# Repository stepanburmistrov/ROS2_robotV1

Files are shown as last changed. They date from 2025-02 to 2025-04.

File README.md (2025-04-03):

# ROS2 Robot: Учебные материалы

Внешний вид робота

Тут собраны учебные материалы и примеры по разработке робота на **ROS2**.

## Изготовление и сборка робота
Робот может быть изготовлен из фанеры толщиной 6мм при помощи лазерной резки, или напечатан на 3д принтере. 
Звенья манипулятора изготавливаются из фанеры 4мм.
- [**Файлы доступны в форматах: SolidWorks 2022, STEP, DXF**](https://github.com/stepanburmistrov/ROS2_robotV1/tree/main/3D)

- [**Подробное описание выбора компонентов, методов сборки и используемых инструментов**](https://stepik.org/lesson/1590256/step/1?unit=1611795)

- [**Электрическая схема робота**](https://github.com/stepanburmistrov/ROS2_robotV1/blob/main/Circuit/ROS2_Robot_Circuit.pdf)
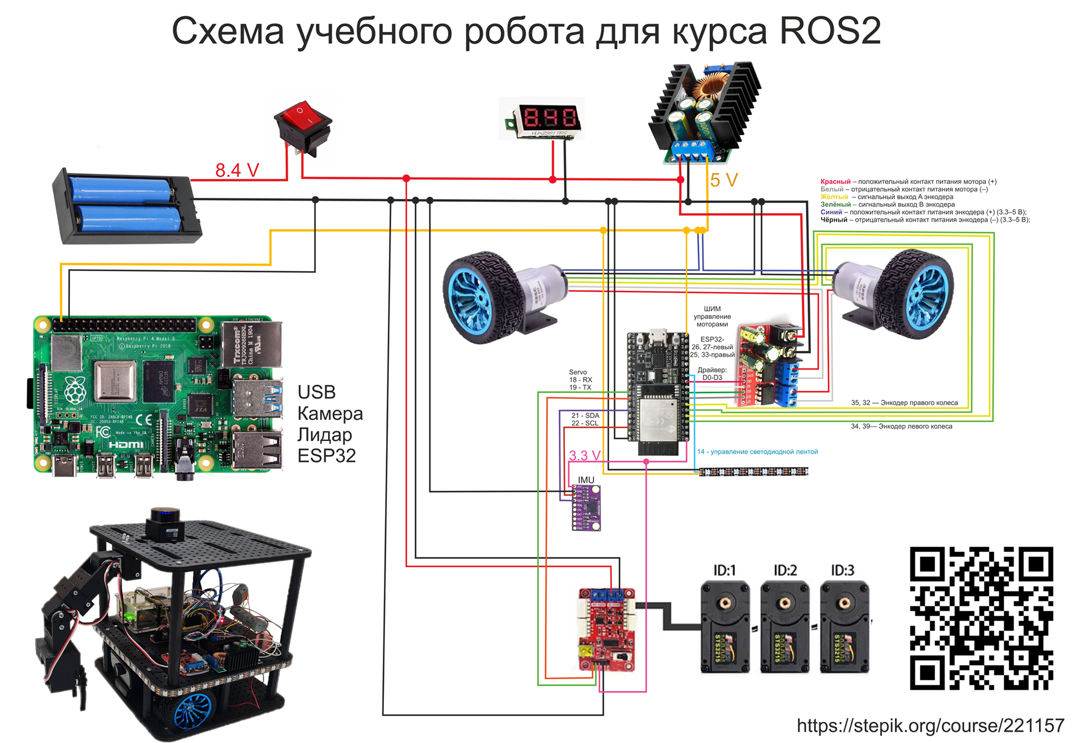
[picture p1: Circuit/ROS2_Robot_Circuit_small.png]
Электрическая схема робота


## Low-level на основе микроконтроллера ESP32
- [**Первые движения робота**](https://stepik.org/lesson/1590257/step/1?unit=1611796)
- [**Кинематика и расчет местоположения**](https://stepik.org/lesson/1590257/step/2?unit=1611796)
- [**Настройка PID-регуляторов**](https://stepik.org/lesson/1590257/step/4?unit=1611796)
- [**Линейная и угловая скорость робота**](https://stepik.org/lesson/1590257/step/7?unit=1611796)
- [**Световая индикация**](https://stepik.org/lesson/1590257/step/10?unit=1611796)
- [**Подключение IMU**](https://stepik.org/lesson/1590257/step/11?unit=1611796)
- [**Работа с сервоприводами манипулятора**](https://stepik.org/lesson/1590257/step/13?unit=1611796)

## Курс по ROS2
[**Бесплатный курс по ROS2**](https://stepik.org/course/221157):
- [**Установка Linux**](https://stepik.org/lesson/1505338/step/1?unit=1525484)
- [**Установка и запуск ROS2 Jazzy**](https://stepik.org/lesson/1505346/step/1?unit=1525492)
- [**Топик, паблишер, подписчик и другие средства коммуникации**](https://stepik.org/lesson/1597035/step/1?unit=1618661)
- [**Связь с LOW-LEVEL**](https://stepik.org/lesson/1590260/step/1?unit=1611799)
- [**RVIZ -  визуализация всего в роботе**](https://stepik.org/lesson/1612393/step/1?unit=1634192)
- [**Gazebo - симулятор робота с физикой**](https://stepik.org/lesson/1612395/step/1?unit=1634194)

Присоединяйтесь к курсу и улучшайте навыки программирования роботов, от базовой сборки до полноценной симуляции и автономной навигации!

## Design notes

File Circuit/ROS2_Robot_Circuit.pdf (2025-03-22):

8.4 V

# Схема учебного робота для курса ROS2

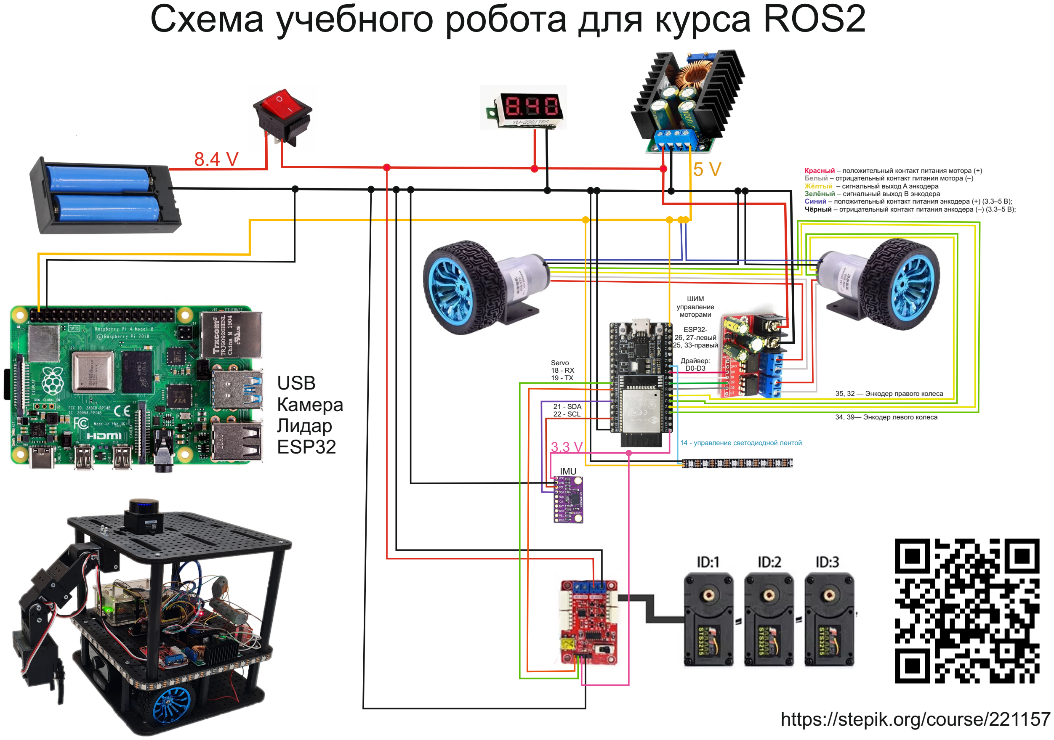
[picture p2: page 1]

ШИМ
управление
моторами

ESP32-
26, 27-левый
25, 33-правый

Драйвер:
D0-D3

34, 39— Энкодер левого колеса

35, 32 — Энкодер правого колеса

5 V | Красный – положительный контакт питания мотора (+)
| Белый – отрицательный контакт питания мотора (–) Жёлтый – сигнальный выход A энкодера Зелёный – сигнальный выход B энкодера Синий – положительный контакт питания энкодера (+) (3.3–5 В); Чёрный – отрицательный контакт питания энкодера (–) (3.3–5 В);

14 - управление светодиодной лентой

21 - SDA
22 - SCL

3.3 V

Servo
18 - RX
19 - TX USB

# Камера Лидар ESP32

## IMU

# https://stepik.org/course/221157

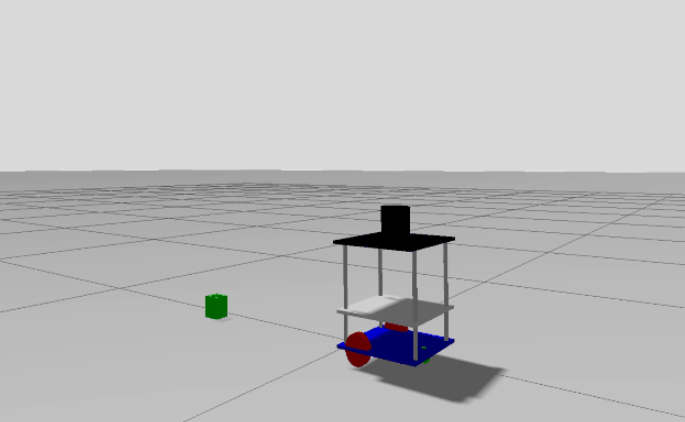
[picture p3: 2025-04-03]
3D/images/gazebo.png

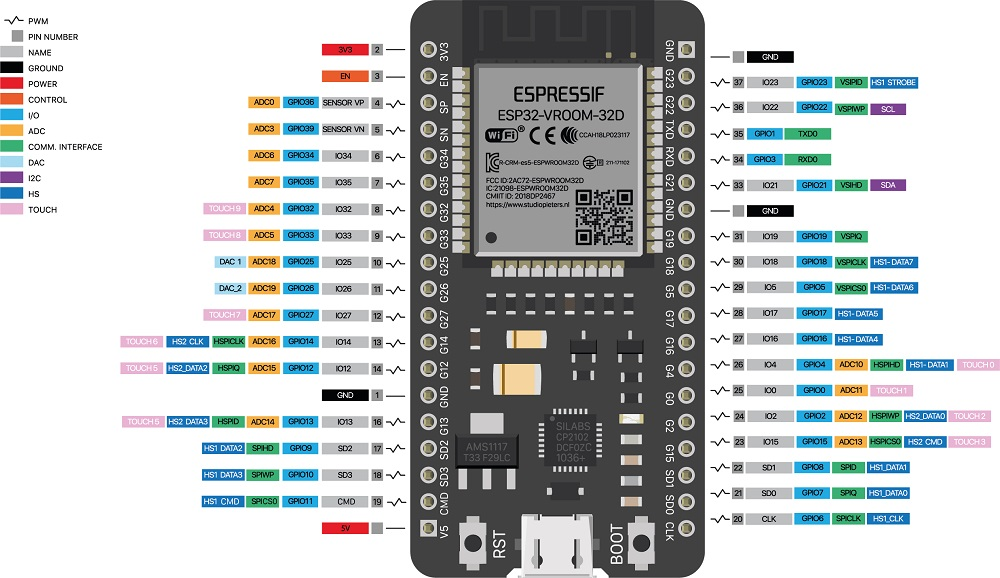
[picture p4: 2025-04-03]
3D/images/image.png

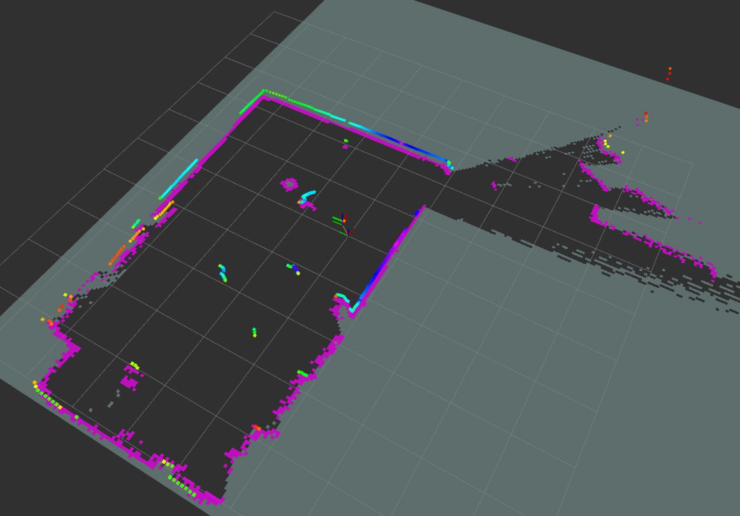
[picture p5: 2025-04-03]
3D/images/esp32.jpg

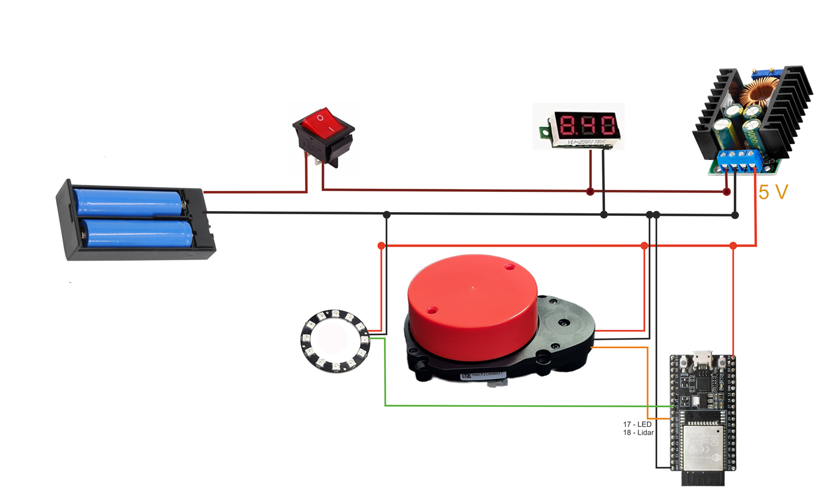
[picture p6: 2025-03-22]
3D/red_lidar_box/RedLidar_Circuit.png

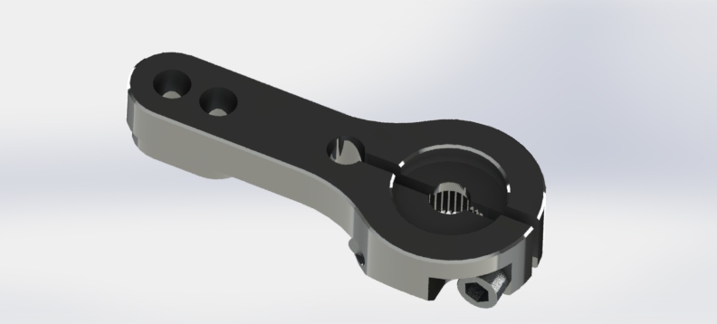
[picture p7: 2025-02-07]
3D/DS3225_MG_metal_horn/View2.JPG

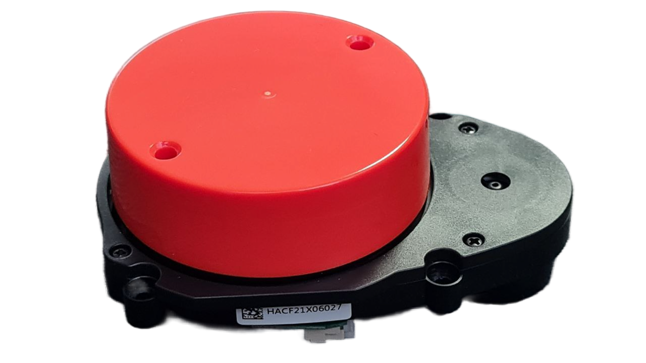
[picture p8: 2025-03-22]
3D/red_lidar_box/lidar.png

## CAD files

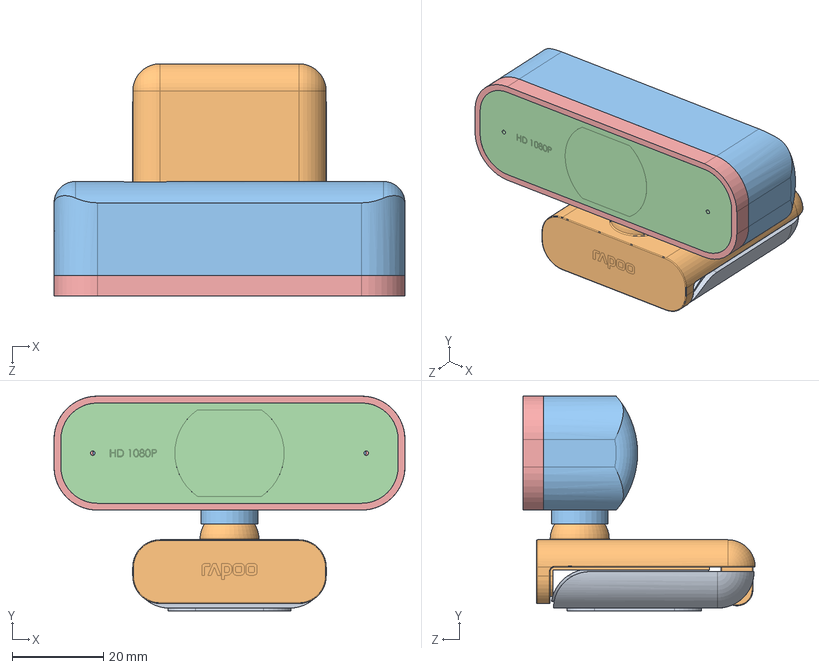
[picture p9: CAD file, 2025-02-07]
3D/webcam/C260 WebCam Assembly.SLDASM
77.0 x 47.1 x 51.0 mm
BaseC
Flexible Holder
Camera Casing
Auto Focus HD 1080p Lens
Lens Support
C260 WebCam
insert round nuts type a gb

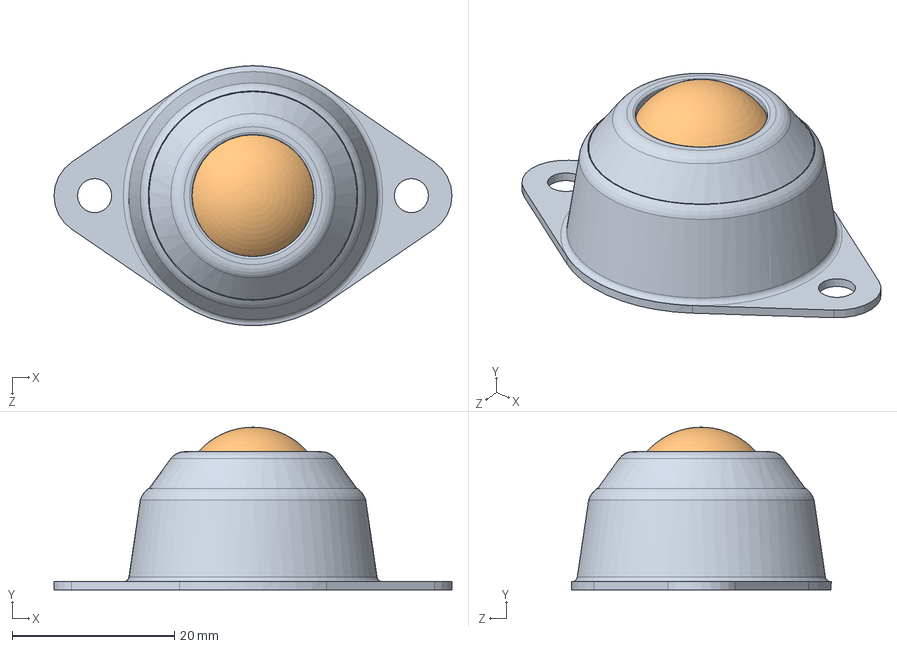
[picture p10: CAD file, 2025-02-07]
3D/Ball/Omni wheel steel ball OW007.SLDASM
49.0 x 20.0 x 32.0 mm
Base
Balle
Fond

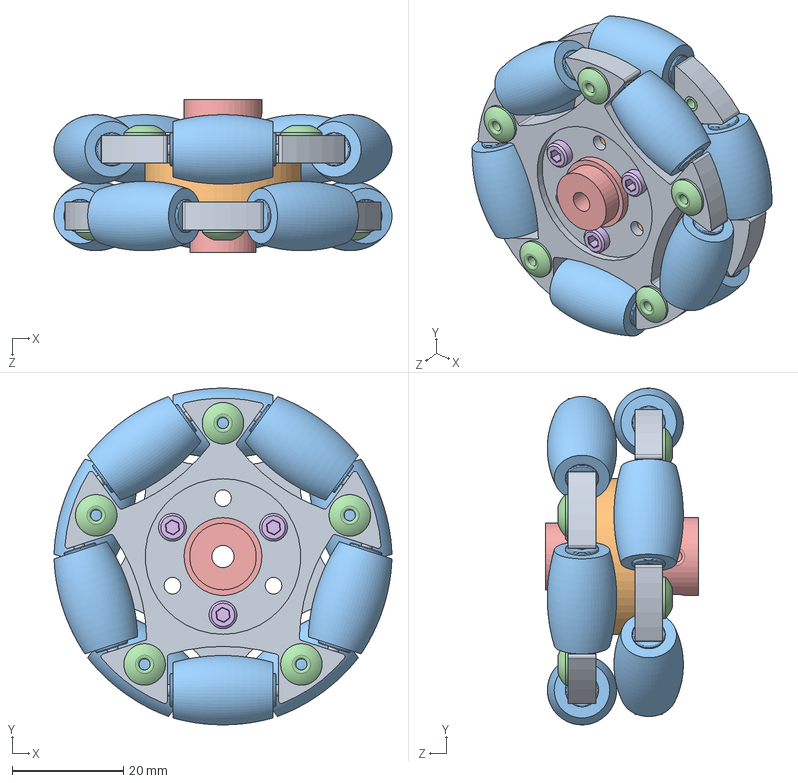
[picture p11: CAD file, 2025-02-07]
3D/Omni/WheelAsm.SLDASM
60.8 x 60.6 x 27.6 mm
WheelBase x 2
BasePlacer
RubberWheel x 10
Rivet x 10
ShaftConnector
M3HexNut x 6

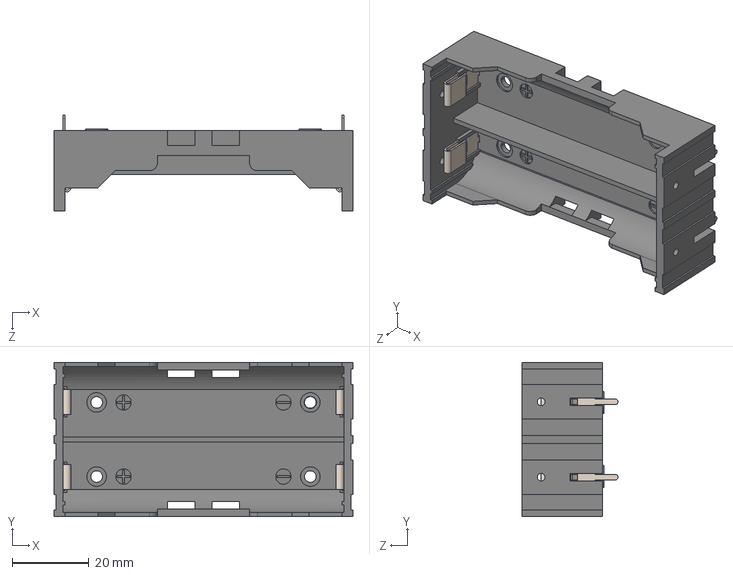
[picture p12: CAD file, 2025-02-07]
3D/18650holder/KLS5-18650-002-D.STEP
77.8 x 40.2 x 25.0 mm
KLS5-18650-002-D_Plastic
KLS5-18650-002-D_Me x 4

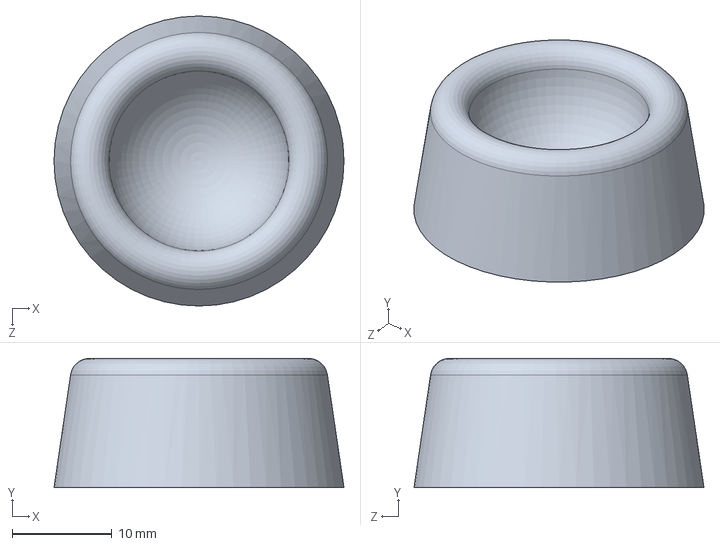
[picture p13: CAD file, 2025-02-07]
3D/Ball/Fond.SLDPRT
29.0 x 12.9 x 29.0 mm

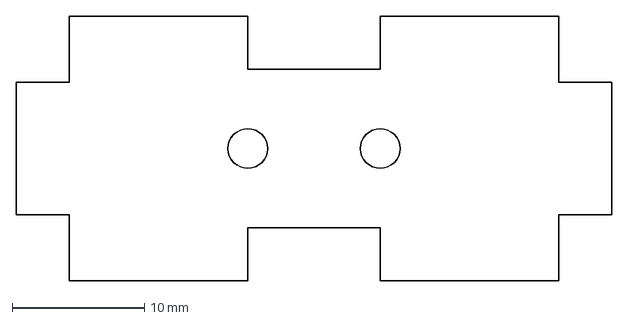
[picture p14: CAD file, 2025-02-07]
3D/dxf/4mm/ServoJointB.dxf
45.0 x 20.0 mm

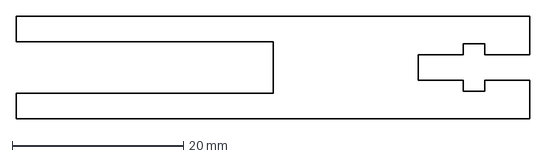
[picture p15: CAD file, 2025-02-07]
3D/dxf/6mm/LayerSupport65.dxf
60.0 x 12.0 mm

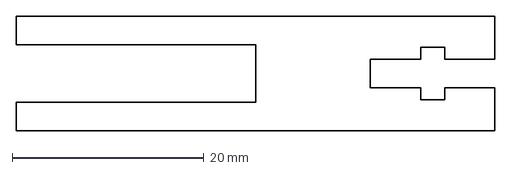
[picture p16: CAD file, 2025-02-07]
3D/dxf/ОпораГайка50.dxf
50.0 x 12.0 mm

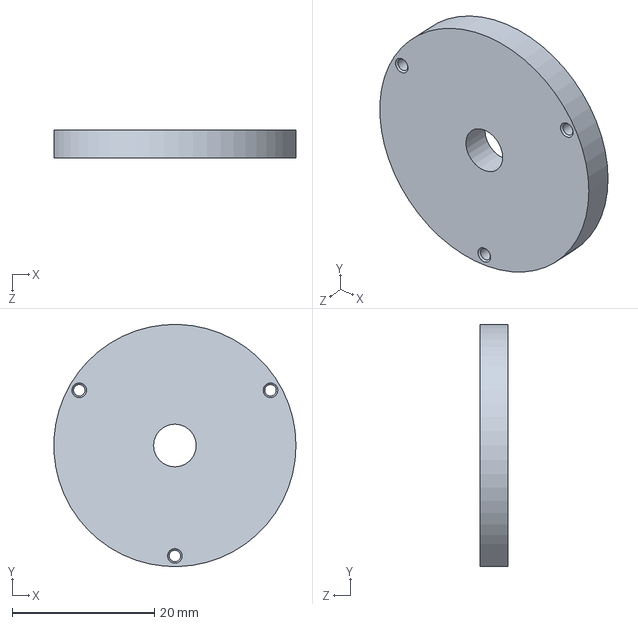
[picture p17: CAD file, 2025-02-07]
3D/jgb37/COUPLING BRACKET, GEARED BODY TO DC MOTOR, JGB37-520.SLDPRT
34.0 x 34.0 x 4.00 mm

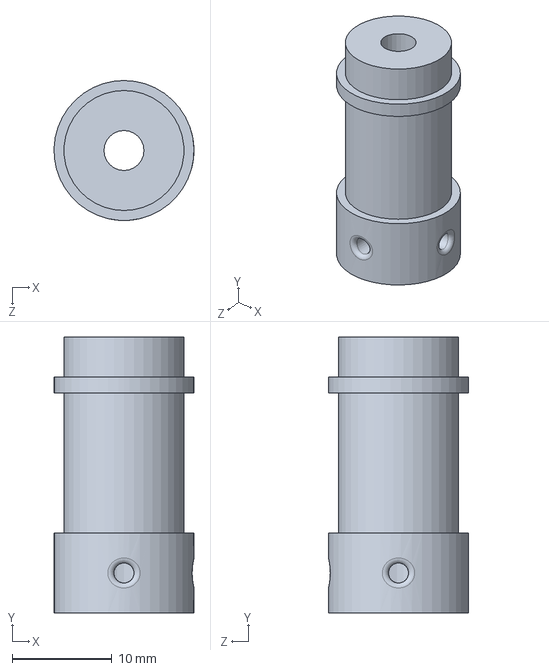
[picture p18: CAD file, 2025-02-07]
3D/Omni/ShaftConnector.SLDPRT
14.0 x 27.6 x 14.0 mm

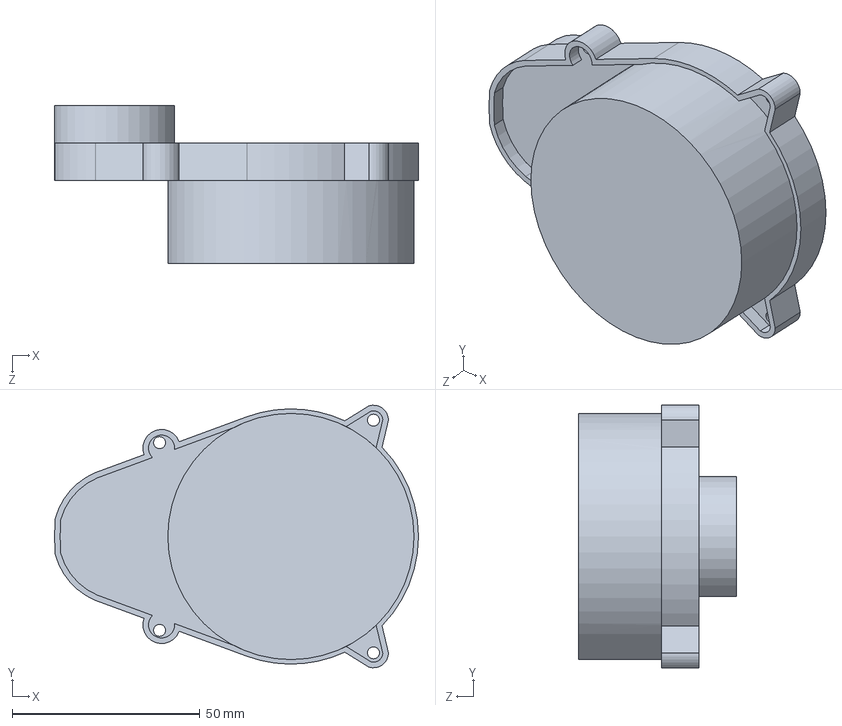
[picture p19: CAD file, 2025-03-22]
3D/red_lidar_box/ydlidar x4.SLDPRT
97.0 x 70.0 x 42.0 mm

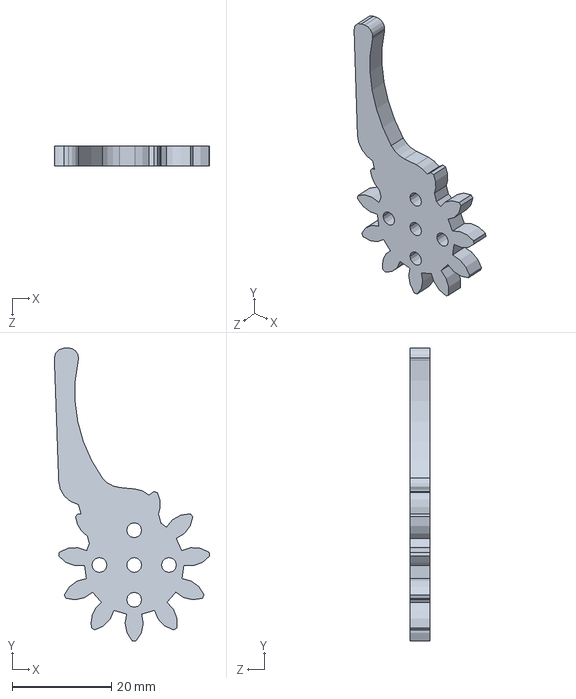
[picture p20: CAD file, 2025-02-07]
3D/STEP/GripperLeftGear.step.SLDPRT
31.3 x 59.0 x 4.00 mm

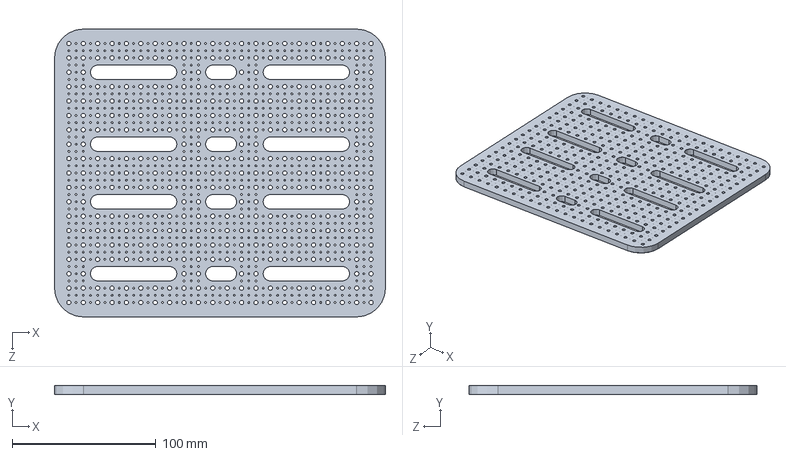
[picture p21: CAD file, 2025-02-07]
3D/TopLayer.SLDPRT
230.0 x 6.00 x 200.0 mm

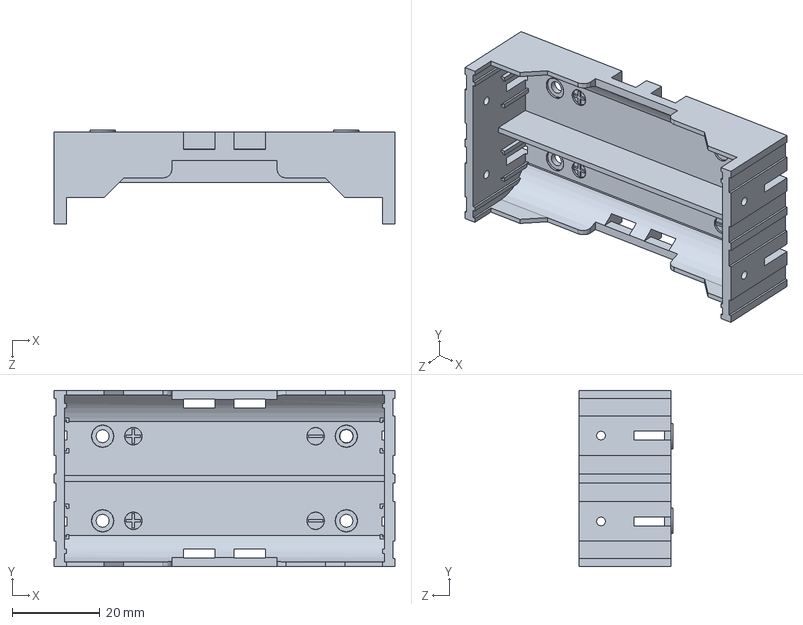
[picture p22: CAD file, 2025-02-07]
3D/18650holder/KLS5-18650-002-D_Plastic.SLDPRT
77.8 x 40.2 x 21.4 mm

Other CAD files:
3D/DS3225_MG_metal_horn/Assembly_DS3225MG_Metal_Horn.SLDASM
3D/Ball/Base.SLDPRT
3D/DS3225_MG_metal_horn/DS3225_MG_metal_horn.STEP
3D/dxf/4mm/BallWheelSupport.dxf
3D/18650holder/KLS5-18650-002-D.SLDASM
3D/18650holder/KLS5-18650-002-D_Me.SLDPRT
3D/Ball/Balle.SLDPRT
3D/BallWheelSupport.SLDPRT
3D/BaseLayer.SLDPRT
3D/DS3225_MG_metal_horn/DS3225_MG_metal_horn.SLDPRT
3D/DS3225_MG_metal_horn/screw_M2x8mm.SLDPRT
3D/DS3225_MG_metal_horn/screw_M2x8mm.STEP
3D/GripperLeftGear.SLDPRT
3D/GripperPlateA.SLDPRT
3D/GripperPlateB.SLDPRT
3D/GripperPlateBack.SLDPRT
3D/GripperPlateBottomSide.SLDPRT
3D/GripperRightGear.SLDPRT
3D/GripperServoHorn.SLDPRT
3D/GripperSide.SLDPRT
3D/L298N.SLDPRT
3D/Layer.SLDPRT
3D/LayerSupport130.SLDPRT
3D/LayerSupport65.SLDPRT
3D/OMNISupport.SLDPRT
3D/Omni/BasePlacer.SLDPRT
3D/Omni/M3HexNut.SLDPRT
3D/Omni/Rivet.SLDPRT
3D/Omni/RubberWheel.SLDPRT
3D/Omni/WheelBase.SLDPRT
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

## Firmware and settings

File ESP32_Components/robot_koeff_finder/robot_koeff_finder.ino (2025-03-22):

// Определение пинов, переменных энкодеров, положения робота и т.д.
#define LEFT_MOTOR_A 27     
#define LEFT_MOTOR_B 26     
#define RIGHT_MOTOR_A 25    
#define RIGHT_MOTOR_B 33    

#define LEFT_ENCODER_A 39    
#define LEFT_ENCODER_B 34    
#define RIGHT_ENCODER_A 32   
#define RIGHT_ENCODER_B 35   

volatile long left_encoder_value = 0; 
volatile long right_encoder_value = 0;
long last_left_encoder = 0;
long last_right_encoder = 0;

long last_speed_left_encoder = 0, last_speed_right_encoder = 0;
float leftWheelSpeed = 0.0, rightWheelSpeed = 0.0;
float vlSpeedFiltered = 0.0, vrSpeedFiltered = 0.0;
uint32_t lastTimeL = 0, lastTimeR = 0;

float targetLeftWheelSpeed = 0, targetRightWheelSpeed = 0;

float xPos = 0.0, yPos = 0.0, theta = 0.0;

const float WHEEL_DIAMETER = 69.0;
const float WHEEL_BASE = 185.0;
const float ENCODER_RESOLUTION = 330.0;
const float TICKS_TO_MM = (PI * WHEEL_DIAMETER) / ENCODER_RESOLUTION;
const float ALPHA = 0.5; // Коэффициент фильтрации скорости

// Глобальные коэффициенты PID – их можно обновлять через UART
float pidKp = 1.1;
float pidKi = 1.3;
float pidKd = 0.01;
float pidKff = 0.25;

void left_interrupt() {
  digitalRead(LEFT_ENCODER_B) ? left_encoder_value++ : left_encoder_value--;
}
void right_interrupt() {
  digitalRead(RIGHT_ENCODER_B) ? right_encoder_value++ : right_encoder_value--;
}

void updateOdometry() {
  long deltaLeft = left_encoder_value - last_left_encoder;
  long deltaRight = right_encoder_value - last_right_encoder;
  last_left_encoder = left_encoder_value;
  last_right_encoder = right_encoder_value;

  float distLeft = deltaLeft * TICKS_TO_MM;
  float distRight = deltaRight * TICKS_TO_MM;
  float deltaS = (distLeft + distRight) / 2.0;
  float deltaTheta = (distRight - distLeft) / WHEEL_BASE;

  theta += deltaTheta;
  xPos += deltaS * cos(theta);
  yPos += deltaS * sin(theta);
}

void computeSpeed() {
  uint32_t now = micros();

  if (lastTimeL == 0 || lastTimeR == 0) { 
    lastTimeL = now;
    lastTimeR = now;
    last_speed_left_encoder = left_encoder_value;
    last_speed_right_encoder = right_encoder_value;
    return;
  }

  float dtL = (now - lastTimeL) * 0.000001;
  float dtR = (now - lastTimeR) * 0.000001;

  if (dtL > 0 && left_encoder_value != last_speed_left_encoder) {
    long deltaLeft = left_encoder_value - last_speed_left_encoder;
    float wlSpeed = ((float)deltaLeft / ENCODER_RESOLUTION) * 360.0f / dtL;
    float vlSpeed = (wlSpeed / 360.0f) * (PI * WHEEL_DIAMETER);
    vlSpeedFiltered = ALPHA * vlSpeed + (1.0f - ALPHA) * vlSpeedFiltered;
    last_speed_left_encoder = left_encoder_value;
    lastTimeL = now;
  } else if (dtL > 0.005 && left_encoder_value == last_speed_left_encoder){
    vlSpeedFiltered = 0;
  }

  if (dtR > 0 && right_encoder_value != last_speed_right_encoder) {
    long deltaRight = right_encoder_value - last_speed_right_encoder;
    float wrSpeed = ((float)deltaRight / ENCODER_RESOLUTION) * 360.0f / dtR;
    float vrSpeed = (wrSpeed / 360.0f) * (PI * WHEEL_DIAMETER);
    vrSpeedFiltered = ALPHA * vrSpeed + (1.0f - ALPHA) * vrSpeedFiltered;
    last_speed_right_encoder = right_encoder_value;
    lastTimeR = now;
  } else if (dtR > 0.005 && right_encoder_value == last_speed_right_encoder){
    vrSpeedFiltered = 0;
  }
}

void computeWheelsPID(){
  // Ограничение интегральной составляющей (anti-windup)
  const float integralLimit = 100.0;

  // Статические переменные для состояния PID для каждого колеса
  static float errorLeftIntegral = 0;
  static float errorRightIntegral = 0;
  static float prevErrorLeft = 0;
  static float prevErrorRight = 0;
  static uint32_t lastPIDTime = millis();
  // Для сброса интегральной составляющей при смене целевой скорости
  static float lastTargetLeft = 0.0;
  static float lastTargetRight = 0.0;

  // Сброс интеграла, если целевая скорость изменилась
  if(targetLeftWheelSpeed != lastTargetLeft){
    errorLeftIntegral = 0;
    prevErrorLeft = 0;
    lastTargetLeft = targetLeftWheelSpeed;
  }
  if(targetRightWheelSpeed != lastTargetRight){
    errorRightIntegral = 0;
    prevErrorRight = 0;
    lastTargetRight = targetRightWheelSpeed;
  }

  // Вычисляем интервал dt (в секундах)
  uint32_t now = millis();
  float dt = (now - lastPIDTime) / 1000.0f;
  if(dt < 0.001f) dt = 0.001f;
  lastPIDTime = now;

  // Расчет ошибок
  float errorLeft  = targetLeftWheelSpeed  - vlSpeedFiltered;
  float errorRight = targetRightWheelSpeed - vrSpeedFiltered;

  // Интегральная составляющая
  errorLeftIntegral  += errorLeft  * dt;
  errorRightIntegral += errorRight * dt;
  if(errorLeftIntegral > integralLimit)  errorLeftIntegral  = integralLimit;
  if(errorLeftIntegral < -integralLimit) errorLeftIntegral  = -integralLimit;
  if(errorRightIntegral > integralLimit)  errorRightIntegral = integralLimit;
  if(errorRightIntegral < -integralLimit) errorRightIntegral = -integralLimit;

  // Производная ошибки
  float derivativeLeft  = (errorLeft  - prevErrorLeft)  / dt;
  float derivativeRight = (errorRight - prevErrorRight) / dt;
  prevErrorLeft  = errorLeft;
  prevErrorRight = errorRight;

  // Вычисление PID-выхода с использованием глобальных коэффициентов
  float pidLeft  = pidKp * errorLeft  + pidKi * errorLeftIntegral  + pidKd * derivativeLeft;
  float pidRight = pidKp * errorRight + pidKi * errorRightIntegral + pidKd * derivativeRight;

  // Добавляем feedforward
  float outputLeft  = pidLeft  + pidKff * targetLeftWheelSpeed;
  float outputRight = pidRight + pidKff * targetRightWheelSpeed;

  // Преобразование в значения ШИМ
  int leftA_PWM = 0, leftB_PWM = 0;
  int rightA_PWM = 0, rightB_PWM = 0;

  if(outputLeft >= 0){
    leftA_PWM = 0;
    leftB_PWM = constrain((int)outputLeft, 0, 255);
  } else {
    leftA_PWM = constrain((int)(-outputLeft), 0, 255);
    leftB_PWM = 0;
  }
  if(outputRight >= 0){
    rightA_PWM = 0;
    rightB_PWM = constrain((int)outputRight, 0, 255);
  } else {
    rightA_PWM = constrain((int)(-outputRight), 0, 255);
    rightB_PWM = 0;
  }

  setMotorsPWM(leftA_PWM, leftB_PWM, rightA_PWM, rightB_PWM);
}

void setMotorsPWM(int leftA, int leftB, int rightA, int rightB) {
  leftA  = constrain(leftA, 0, 255);
  leftB  = constrain(leftB, 0, 255);
  rightA = constrain(rightA, 0, 255);
  rightB = constrain(rightB, 0, 255);

  analogWrite(LEFT_MOTOR_A, leftA);
  analogWrite(LEFT_MOTOR_B, leftB);
  analogWrite(RIGHT_MOTOR_A, rightA);
  analogWrite(RIGHT_MOTOR_B, rightB);
}

// Функция для парсинга команды установки коэффициентов: "SET_COEFF Kp Ki Kd Kff"
bool parseSetCoeff(const String& command, float* Kp, float* Ki, float* Kd, float* Kff) {
  int index1 = command.indexOf(' ');
  if(index1 == -1) return false;
  int index2 = command.indexOf(' ', index1 + 1);
  if(index2 == -1) return false;
  int index3 = command.indexOf(' ', index2 + 1);
  if(index3 == -1) return false;
  int index4 = command.indexOf(' ', index3 + 1);
  if(index4 == -1) return false;

  *Kp = command.substring(index1 + 1, index2).toFloat();
  *Ki = command.substring(index2 + 1, index3).toFloat();
  *Kd = command.substring(index3 + 1, index4).toFloat();
  *Kff = command.substring(index4 + 1).toFloat();
  return true;
}

// Другие функции парсинга команд (SET_PWM, SET_POSE, SET_WHEELS_SPEED) аналогичны предыдущим примерам
bool parseSetPWM(const String& command, int* leftA_PWM, int* leftB_PWM, int* rightA_PWM, int* rightB_PWM) {
  int index1 = command.indexOf(' ');
  if (index1 == -1) return false;
  int index2 = command.indexOf(' ', index1 + 1);
  if (index2 == -1) return false;
  int index3 = command.indexOf(' ', index2 + 1);
  if (index3 == -1) return false;
  int index4 = command.indexOf(' ', index3 + 1);
  if (index4 == -1) return false;

  *leftA_PWM = command.substring(index1 + 1, index2).toInt();
  *leftB_PWM = command.substring(index2 + 1, index3).toInt();
  *rightA_PWM = command.substring(index3 + 1, index4).toInt();
  *rightB_PWM = command.substring(index4 + 1).toInt();
  return true;
}
bool parseSetSpeed(const String& command, int* speedLeft, int* speedRight) {
  int index1 = command.indexOf(' ');
  if (index1 == -1) return false;
  int index2 = command.indexOf(' ', index1 + 1);
  if (index2 == -1) return false;

  *speedLeft = command.substring(index1 + 1, index2).toInt();
  *speedRight = command.substring(index2 + 1).toInt();
  return true;
}

void processCommand(String command) {
  command.trim();
  if (command.startsWith("SET_PWM")) {
    int leftA_PWM = 0, leftB_PWM = 0, rightA_PWM =0, rightB_PWM = 0;
    if (parseSetPWM(command, &leftA_PWM, &leftB_PWM, &rightA_PWM, &rightB_PWM)) {
      setMotorsPWM(leftA_PWM, leftB_PWM, rightA_PWM, rightB_PWM);
      Serial.println("OK: Set PWM");
    }
  } else if (command.startsWith("SET_POSE")) {
    float x, y, th;
    // Парсинг команды SET_POSE аналогичен предыдущему примеру
    // …
    Serial.println("OK: Pose set");
  } else if (command.startsWith("SET_WHEELS_SPEED")) {
    int leftSpeed = 0, rightSpeed = 0;
    if (parseSetSpeed(command, &leftSpeed, &rightSpeed)) {
      targetLeftWheelSpeed = leftSpeed;
      targetRightWheelSpeed = rightSpeed;
      Serial.println("OK: Wheel speed set");
    }
  } else if (command.startsWith("SET_COEFF")) {
    float newKp, newKi, newKd, newKff;
    if (parseSetCoeff(command, &newKp, &newKi, &newKd, &newKff)) {
      pidKp = newKp;
      pidKi = newKi;
      pidKd = newKd;
      pidKff = newKff;
      Serial.println("OK: Coefficients updated");
    } else {
      Serial.println("ERROR: Invalid coefficients");
    }
  } else {
    Serial.println("ERROR: Unknown command");
  }
}

void setup() {
  Serial.begin(115200);
  delay(1000);
  Serial.println("System started");

  attachInterrupt(digitalPinToInterrupt(LEFT_ENCODER_A), left_interrupt, RISING);
  attachInterrupt(digitalPinToInterrupt(RIGHT_ENCODER_A), right_interrupt, RISING);
  
  pinMode(LEFT_MOTOR_A, OUTPUT);
  pinMode(LEFT_MOTOR_B, OUTPUT);
  pinMode(RIGHT_MOTOR_A, OUTPUT);
  pinMode(RIGHT_MOTOR_B, OUTPUT);
  
  pinMode(LEFT_ENCODER_A, INPUT);
  pinMode(LEFT_ENCODER_B, INPUT);
  pinMode(RIGHT_ENCODER_A, INPUT);
  pinMode(RIGHT_ENCODER_B, INPUT);
}

void loop() {
  if (Serial.available()) {
    String command = Serial.readStringUntil('\n');
    processCommand(command);
  }
  

  static uint32_t PIDTimer = 0;
  if (millis() - PIDTimer > 50) {
    computeSpeed();
    updateOdometry();
    computeWheelsPID();
    PIDTimer = millis();
  }

  static uint32_t printTimer = 0;
  if (millis() - printTimer > 200) {
    Serial.printf("POS X=%.2f Y=%.2f Th=%.2f ", xPos, yPos, theta);
    Serial.printf("ENC L=%ld R=%ld ", left_encoder_value, right_encoder_value);
    Serial.printf("SPD L=%.2f mm/s R=%.2f mm/s ", vlSpeedFiltered, vrSpeedFiltered);
    Serial.printf("Target L=%.2f mm/s R=%.2f mm/s\n", targetLeftWheelSpeed, targetRightWheelSpeed);
    printTimer = millis();
  }
}

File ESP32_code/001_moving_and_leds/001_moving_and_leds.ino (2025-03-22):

#include <Adafruit_NeoPixel.h>
#include <SCServo.h>
// Класс для управления STS-сервами (FEETECH STS3215 и т.д.)
SMS_STS st;

// Пины UART (приведён пример для ESP32 с UART1, GPIO 18/19).
#define S_RXD 18
#define S_TXD 19

// Скорость UART для серво
#define SERVO_BAUD 1000000

// ------------------------- НАСТРОЙКИ СВЕТОДИОДНОЙ ЛЕНТЫ -------------------------
#define PIN_WS2812B 14     // Пин, к которому подключена лента
#define NUM_PIXELS 50      // Кол-во светодиодов в ленте
#define LED_BRIGHTNESS 50  // Базовая «глобальная» яркость (0-255), если нужно

Adafruit_NeoPixel ws2812b(NUM_PIXELS, PIN_WS2812B, NEO_GRB + NEO_KHZ800);

uint8_t bootMode = 1;
// ---------------------------------------------------------------------------------

/****************************************************************************
 * Определение пинов, переменных энкодеров, положения робота и т.д.
 ***************************************************************************/
#define LEFT_MOTOR_A 27
#define LEFT_MOTOR_B 26
#define RIGHT_MOTOR_A 25
#define RIGHT_MOTOR_B 33

#define LEFT_ENCODER_A 39
#define LEFT_ENCODER_B 34
#define RIGHT_ENCODER_A 32
#define RIGHT_ENCODER_B 35

volatile long left_encoder_value = 0;
volatile long right_encoder_value = 0;
long last_left_encoder = 0;
long last_right_encoder = 0;

long last_speed_left_encoder = 0, last_speed_right_encoder = 0;
float vlSpeedFiltered = 0.0, vrSpeedFiltered = 0.0;
uint32_t lastTimeL = 0, lastTimeR = 0;

float targetLeftWheelSpeed = 0, targetRightWheelSpeed = 0;

float xPos = 0.0, yPos = 0.0, theta = 0.0;

const float WHEEL_DIAMETER = 69.0;       // мм
const float WHEEL_BASE = 185.0;          // мм (расстояние между центрами колёс)
const float ENCODER_RESOLUTION = 330.0;  // тиков на оборот
const float TICKS_TO_MM = (PI * WHEEL_DIAMETER) / ENCODER_RESOLUTION;
const float ALPHA = 0.5;  // Коэффициент экспоненциальной фильтрации скорости

// Глобальные коэффициенты PID – их можно обновлять через UART
float pidKp = 1.1;
float pidKi = 1.3;
float pidKd = 0.01;
float pidKff = 0.25;

// Глобальные PID-состояния
float errorLeftIntegral = 0;
float errorRightIntegral = 0;
float prevErrorLeft = 0;
float prevErrorRight = 0;
uint32_t lastPIDTime = 0;

// Функция сброса PID-переменных (интегральная и дифференциальная составляющие, а также фильтрованные скорости)
void resetPID() {
  errorLeftIntegral = 0;
  errorRightIntegral = 0;
  prevErrorLeft = 0;
  prevErrorRight = 0;
  vlSpeedFiltered = 0;
  vrSpeedFiltered = 0;
  lastPIDTime = millis();
}

/****************************************************************************
 * Переменные компенсации прямолинейного движения
 ***************************************************************************/
bool goingStraight = false;  // Флаг, указывающий, что робот едет прямо (угловая скорость ≈ 0)
long leftBase = 0;           // Значение left_encoder_value в момент начала прямолинейного движения
long rightBase = 0;          // Значение right_encoder_value в момент начала прямолинейного движения

/****************************************************************************
 * Прерывания энкодеров
 ***************************************************************************/
void left_interrupt() {
  digitalRead(LEFT_ENCODER_B) ? left_encoder_value++ : left_encoder_value--;
}
void right_interrupt() {
  digitalRead(RIGHT_ENCODER_B) ? right_encoder_value++ : right_encoder_value--;
}

/****************************************************************************
 * Одометрия
 ***************************************************************************/
void updateOdometry() {
  long deltaLeft = left_encoder_value - last_left_encoder;
  long deltaRight = right_encoder_value - last_right_encoder;
  last_left_encoder = left_encoder_value;
  last_right_encoder = right_encoder_value;

  float distLeft = deltaLeft * TICKS_TO_MM;
  float distRight = deltaRight * TICKS_TO_MM;
  float deltaS = (distLeft + distRight) / 2.0;
  float deltaTheta = (distRight - distLeft) / WHEEL_BASE;

  theta += deltaTheta;
  xPos += deltaS * cos(theta);
  yPos += deltaS * sin(theta);
}

/****************************************************************************
 * Вычисление скорости колес
 ***************************************************************************/
void computeSpeed() {
  uint32_t now = micros();
  if (lastTimeL == 0 || lastTimeR == 0) {
    lastTimeL = now;
    lastTimeR = now;
    last_speed_left_encoder = left_encoder_value;
    last_speed_right_encoder = right_encoder_value;
    return;
  }
  float dtL = (now - lastTimeL) * 1e-6f;
  float dtR = (now - lastTimeR) * 1e-6f;

  if (dtL > 0 && left_encoder_value != last_speed_left_encoder) {
    long deltaLeft = left_encoder_value - last_speed_left_encoder;
    float wlSpeed = ((float)deltaLeft / ENCODER_RESOLUTION) * 360.0f / dtL;
    float vlSpeed = (wlSpeed / 360.0f) * (PI * WHEEL_DIAMETER);
    vlSpeedFiltered = ALPHA * vlSpeed + (1.0f - ALPHA) * vlSpeedFiltered;
    last_speed_left_encoder = left_encoder_value;
    lastTimeL = now;
  } else if (dtL > 0.005 && left_encoder_value == last_speed_left_encoder) {
    vlSpeedFiltered = 0;
  }
  if (dtR > 0 && right_encoder_value != last_speed_right_encoder) {
    long deltaRight = right_encoder_value - last_speed_right_encoder;
    float wrSpeed = ((float)deltaRight / ENCODER_RESOLUTION) * 360.0f / dtR;
    float vrSpeed = (wrSpeed / 360.0f) * (PI * WHEEL_DIAMETER);
    vrSpeedFiltered = ALPHA * vrSpeed + (1.0f - ALPHA) * vrSpeedFiltered;
    last_speed_right_encoder = right_encoder_value;
    lastTimeR = now;
  } else if (dtR > 0.005 && right_encoder_value == last_speed_right_encoder) {
    vrSpeedFiltered = 0;
  }
}
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
